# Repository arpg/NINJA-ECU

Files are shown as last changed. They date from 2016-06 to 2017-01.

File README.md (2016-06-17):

# NINJA-ECU
ECU board in order to control sensors and actuators of ARPG's self driving vehicle
## How board versions work?
each ECU pcb has a version format of **v.**_X_**.**_Y_ in which
* X represents the major change in functionality of the board
* Y represents minor changes like fixing errors in PCB or adding simple functions like an LED

## How to add a new board with major change?
* branch from current master (this should only add some readme files and folders)
* create your project in the folders created from previous step
* when you are ready to push your changes,create a new branch and name it as 'v.major_number' (ex. **v.3** )
* after you are done with your design add a minor tag of 1 to your last commit (ex. add tag **v.3.1**)

## How to add minor changes for last major board?
* apply andd commit your changes when you were done add a minor tag for your commit (ex. add tag **v.3.2**)

## What should every last minor commit include?
* updated pcbproject, schematic and layout files
* updated gerber files
* updated nc-drill files
* updated assembly files
* updated BOM
* updated pdf showing all schematic and layout files

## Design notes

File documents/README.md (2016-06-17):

# Documents
## what should be in this folder?
* a pdf documet showing all the schematics of the project and a 1:1 scaled layout with all layers

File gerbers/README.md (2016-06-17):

# Gerber Files
## what should be in this folder?
this folder should include all the gerber files and nc-drill files for the project

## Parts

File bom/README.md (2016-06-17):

# Bill Of Material
## what should be in this folder?
this folder includes a list of components with their designator, value, digikey part number, quantity and a short comment
try to use the template from ARPGPCBLib

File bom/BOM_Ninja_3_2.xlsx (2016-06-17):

Comment | Quantity | Designator | Manufacturer Part Number 1 | Supplier 1 | Supplier Part Number 1
Terminal3, Terminal2, Terminal2 | 3 | BLDC1, PWR1_BATT, PWR2_COMP |  |  | DNI
18pF | 2 | C1, C3 | 251R14S180GV4T | Digi-Key | 712-1321-1-ND
2.2uF | 9 | C2, C4, C6, C7, C25, C30, C34, C39, C46 | F981A225MMA | Digi-Key | 478-8647-1-ND
100nF | 23 | C5, C8, C9, C10, C11, C20, C21, C22, C35, C44, C48, C56, C63, C64, C65, C66, C67, C68, C69, C70, C71, C72, C73 | CC0603KRX7R7BB104 | Digi-Key | 311-1088-1-ND
15pF | 2 | C12, C13 | 251R14S150JV4T | Digi-Key | 712-1318-1-ND
4.7nF | 4 | C14, C15, C16, C17 | C1608C0G1E472J080AA | Digi-Key | 445-2712-1-ND
10uF | 5 | C18, C47, C49, C50, C54 | TAJC106M016RNJ | Digi-Key | 478-1702-1-ND
150uF | 1 | C19 | TCJW157M006R0070 | Digi-Key | 478-3481-1-ND
100uF | 1 | C23 | NOJC107M004RWJ | Digi-Key | 478-1824-1-ND
330uF | 1 | C24 | TAJC337M006RNJ | Digi-Key | 478-8902-1-ND
100pF | 2 | C26, C41 | C0603C101J5GACTU | Digi-Key | 399-1061-1-ND
150uF/6.3V | 1 | C27 | TCJW157M006R0070 | Digi-Key | 478-3481-1-ND
1000uF/16V | 2 | C28, C31 | UCL1C102MNL1GS | Digi-Key | 493-3930-1-ND
1nF | 2 | C29, C42 | GRM188R71H102KA01D | Digi-Key | 490-1494-1-ND
10nF | 2 | C32, C45 | CC0603KRX7R9BB103 | Digi-Key | 311-1085-1-ND
6.8nF | 1 | C33 | C1608C0G1E682J080AA | Digi-Key | 445-2667-1-ND
120pF | 1 | C36 | C0603C121J5GACTU | Digi-Key | 399-1062-1-ND
22nF | 1 | C38 | C0603C223K1RACTU | Digi-Key | 399-3476-1-ND
100uF/16V | 1 | C40 | TPSC107K010R0150 | Digi-Key | 478-7995-1-ND
15nF | 1 | C43 | C0603C153J3GACTU | Digi-Key | 399-10044-1-ND
220nF | 3 | C51, C52, C53 | C1608X7R1C224K080AC | Digi-Key | 445-1318-1-ND
220uF/16V | 1 | C55 | TPSC227K006R0125 | Digi-Key | 478-1768-1-ND
100uF | 1 | C57 | TPSC107K010R0150 | Digi-Key | 478-7995-1-ND
4.7uF | 2 | C58, C60 | TAJC475K035RNJ | Digi-Key | 478-1717-1-ND
27pF | 2 | C59, C62 | C0603C270F5GACTU | Digi-Key | 399-7888-1-ND
3.3uF | 1 | C61 | C1608X5R1A335K080AC | Digi-Key | 445-5168-1-ND
2.2nF | 1 | C74 | GRM1885C1H222JA01D | Digi-Key | 490-1459-1-ND
1N5821 | 2 | D1, D3 | 1N5821G |  | DNI
1N5819 | 1 | D2 | 1N5819HW-7-F | Digi-Key | 1N5819HW-FDICT-ND
Enc3, Enc2, Enc1, Enc4, USB1 | 5 | H1, H2, H3, H11, H19 | 0533980471 | Digi-Key | WM7608CT-ND
JTAG | 1 | H4 | 20021121-00010C4LF | Digi-Key | 609-3695-1-ND
Serv1, P_Servo, Serv2, Serv3, Serv4 | 5 | H5, H6, H13, H14, H15 |  |  | DNI
Pot1, Pot2, Pot3, Pot4, Pot5, Pot6, Oc1 | 7 | H7, H8, H9, H10, H12, H16, H17 | 0533980371 | Digi-Key | WM7607CT-ND
Hall Sens1, GPS_Con | 2 | H18, H20 | B6B-ZR-SM4-TF(LF)(SN) | Digi-Key | 455-1685-1-ND
IMU_Con | 1 | H21 | 0533980671 | Digi-Key | WM7610CT-ND
10uH | 2 | L1, L2 | LBR2012T100K | Digi-Key | 587-2045-1-ND
100uH | 1 | L3 | SDR0805-101KL | Digi-Key | SDR0805-101KLCT-ND
22uH | 1 | L4 | SDR0805-220ML | Digi-Key | SDR0805-220MLCT-ND
?H | 2 | L5, L6 | FBMJ2125HL8R0NT | Digi-Key | 587-1764-1-ND
LEDR | 3 | LED1, LED5, LED6 | LS R976-NR-1 | Digi-Key | 475-1278-1-ND
LEDY | 2 | LED2, LED4 | LY R976-PS-36 | Digi-Key | 475-2560-1-ND
LEDG | 1 | LED3 | LG R971-KN-1 | Digi-Key | 475-1410-1-ND
IRFS7530 | 6 | Q1, Q2, Q3, Q4, Q5, Q6 | IRFS7530-7PPBF | Digi-Key | IRFS7530-7PPBF-ND
120 | 10 | R1, R2, R3, R4, R9, R10, R17, R21, R69, R70 | RMCF0603JT120R | Digi-Key | RMCF0603JT120RCT-ND
4.7K | 4 | R5, R6, R7, R61 | ERJ-3GEYJ472V | Digi-Key | P4.7KGCT-ND
1K | 4 | R8, R63, R84, R85 | ERJ-3GEYJ102V | Digi-Key | P1.0KGCT-ND
180 | 6 | R11, R13, R15, R18, R23, R30 | RMCF0603JT180R | Digi-Key | RMCF0603JT180RCT-ND
330 | 12 | R12, R14, R16, R19, R24, R28, R29, R31, R41, R42, R43, R68 | RC0603JR-07330RL | Digi-Key | 311-330GRCT-ND
470 | 5 | R20, R22, R33, R35, R87 | RC0603JR-07470RL | Digi-Key | 311-470GRCT-ND
10K | 12 | R25, R26, R27, R44, R45, R46, R48, R50, R58, R59, R60, R62 | ERJ-3GEYJ103V | Digi-Key | P10KGCT-ND
2.2K | 4 | R32, R34, R36, R57 | RMCF0603JT2K20 | Digi-Key | RMCF0603JT2K20CT-ND
560 | 2 | R37, R67 | RC0603FR-07560RL | Digi-Key | 311-560HRCT-ND
510K | 1 | R38 | ERJ-3EKF5103V | Digi-Key | P510KHCT-ND
90.9K | 1 | R39 | ERJ-3EKF9092V | Digi-Key | P90.9KHCT-ND
3.09K | 1 | R40 | ERJ-3EKF3091V | Digi-Key | P3.09KHCT-ND
330K | 1 | R47 | ERJ-3GEYJ334V | Digi-Key | P330KGCT-ND
15K | 1 | R49 | RMCF0603JT15K0 | Digi-Key | RMCF0603JT15K0CT-ND
220K | 1 | R51 | ERJ-3GEYJ224V | Digi-Key | P220KGCT-ND
3.3K | 1 | R52 | RMCF0603JT3K30 | Digi-Key | RMCF0603JT3K30CT-ND
18K | 2 | R53, R56 | RMCF0603JT18K0 | Digi-Key | RMCF0603JT18K0CT-ND
1M | 2 | R54, R55 | ERJ-3EKF1004V | Digi-Key | P1.00MHCT-ND
12K | 1 | R64 | RC0603JR-0712KL | Digi-Key | 311-12KGRCT-ND
DNI | 2 | R65, R66 |  |  | DNI
4.7 | 6 | R71, R72, R75, R77, R80, R81 | RC0603JR-074R7L | Digi-Key | 311-4.7GRCT-ND
39K | 6 | R73, R74, R76, R78, R82, R83 | RC0603FR-0739KL | Digi-Key | 311-39.0KHRDKR-ND
0.001 | 2 | R79, R86 | WSLP59311L000FEB | Digi-Key | WSLPD-.001CT-ND
SW_TACT | 1 | S1 | PTS645SH50SMTR92 LFS | Digi-Key | CKN9085CT-ND
BC817 | 2 | T1, T2 | BC817-25LT1G | Digi-Key | BC817-25LT1GOSCT-ND
STM32F207VCT6 | 1 | U1 | STM32F207VCT6 | Digi-Key | 497-11170-ND
DRV8302 | 1 | U2 | DRV8302DCAR | Digi-Key | 296-29544-6-ND
1117-3.3 | 2 | U3, U5 | LM1117IMPX-3.3/NOPB | Digi-Key | LM1117IMPX-3.3/NOPBCT-ND
LTM8026 | 1 | U4 | LTM8026EV#PBF | Digi-Key | LTM8026EV#PBF-ND
AT93C46DN-SP25-B | 1 | U6 | AT93C46DN-SH-B | Digi-Key | AT93C46DN-SH-B-ND
FT4232HQ-Reel | 1 | U7 | FT4232HQ-REEL | Digi-Key | 768-1027-1-ND
MAX3485 | 1 | U8 | MAX3485CSA+ | Digi-Key | MAX3485CSA+-ND
MPU9150 | 1 | U9 | MPU-9150 | Digi-Key | 1428-1009-1-ND
8MHz | 1 | X1 | ABM7-8.000MHZ-D2Y-T | Digi-Key | 535-9831-1-ND
32768 Hz | 1 | X2 | ABS06-107-32.768KHZ-T | Digi-Key | 535-12373-1-ND
12MHz | 1 | X3 | ABM7-12.000MHZ-B4-T | Digi-Key | 535-13457-1-ND

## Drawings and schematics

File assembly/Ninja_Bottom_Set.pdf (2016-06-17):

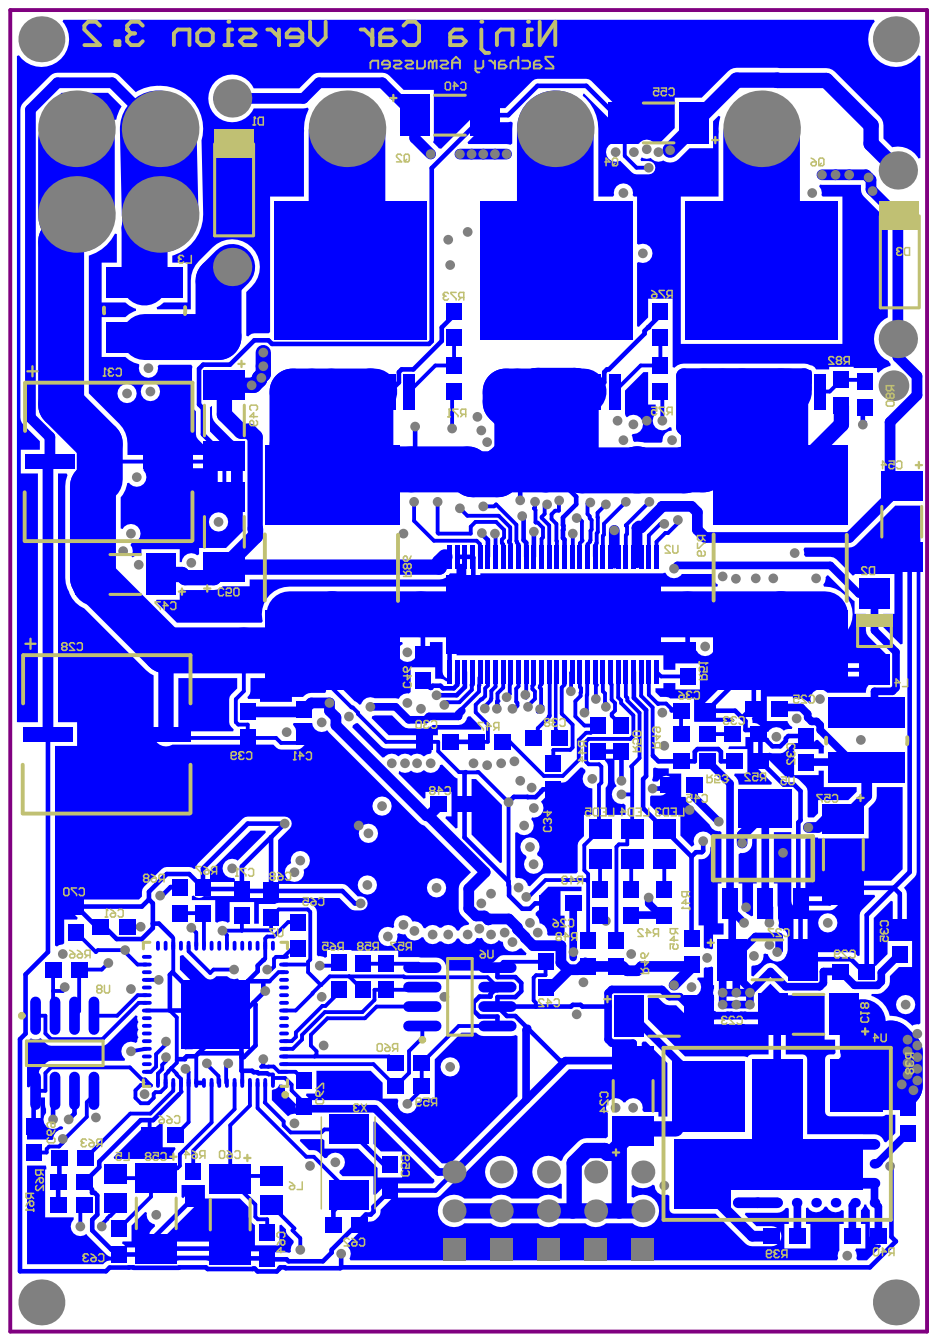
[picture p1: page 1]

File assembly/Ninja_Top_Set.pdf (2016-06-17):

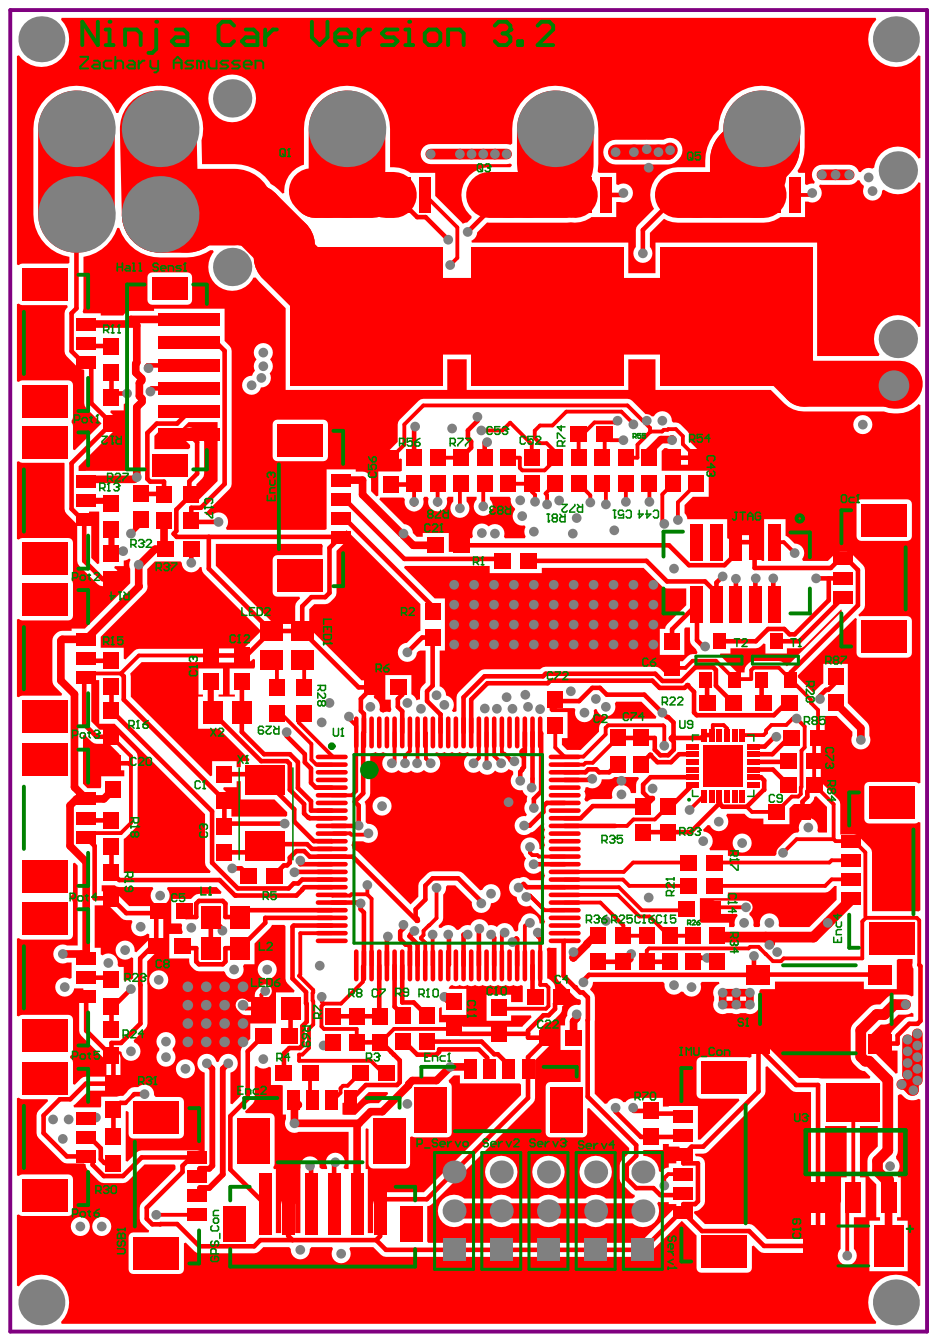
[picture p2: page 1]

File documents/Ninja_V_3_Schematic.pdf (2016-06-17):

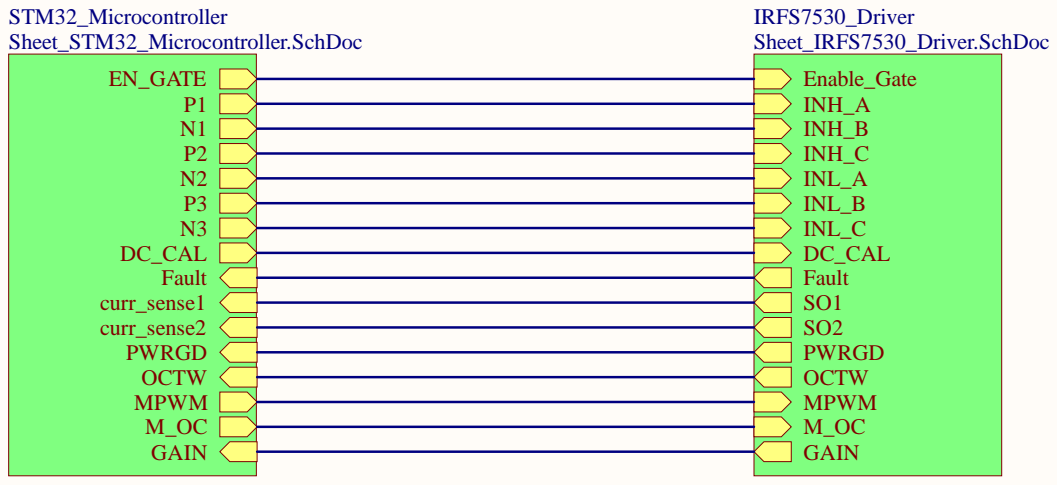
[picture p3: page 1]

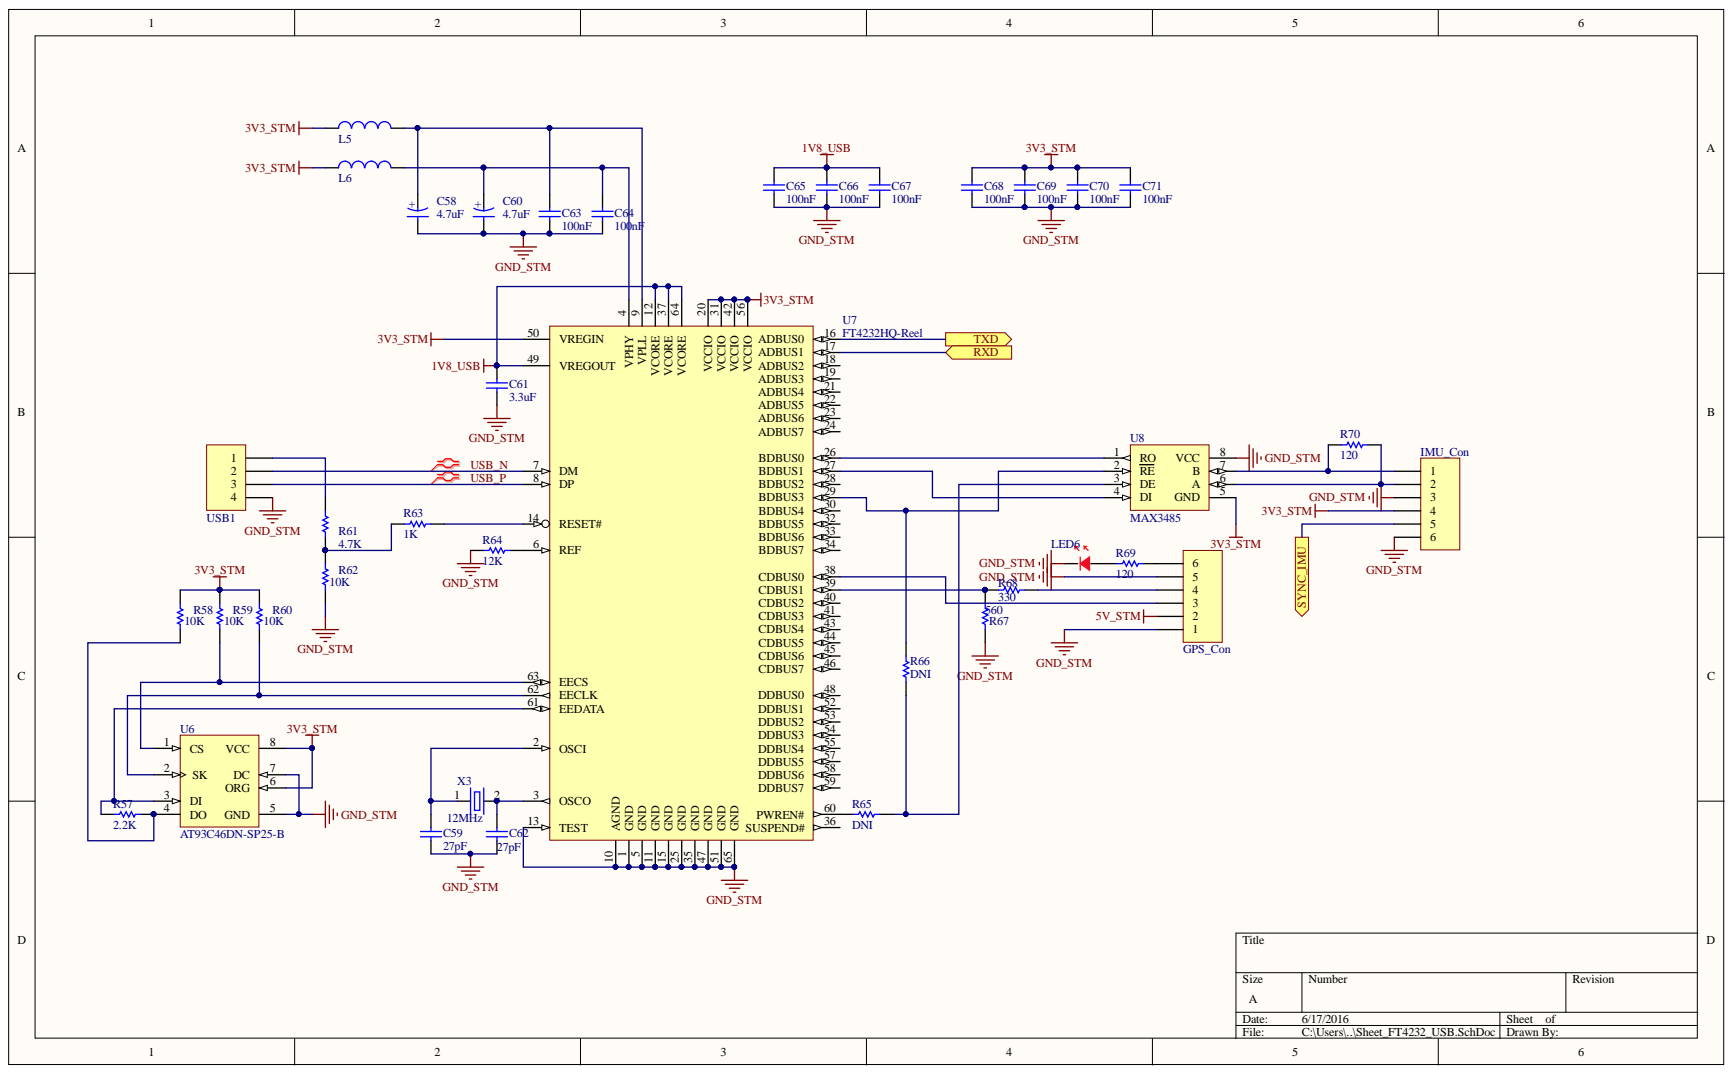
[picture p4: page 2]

EECLK 62
EEDATA 61

U6 3V3_STM | OSCI 2

SK 2 ORG | 6 DC 7 | | OSCO 3

Size A | Number | Revision

Date: 6/17/2016 | Sheet of
File: C:\Users\..\Sheet_FT4232_USB.SchDoc | Drawn By:

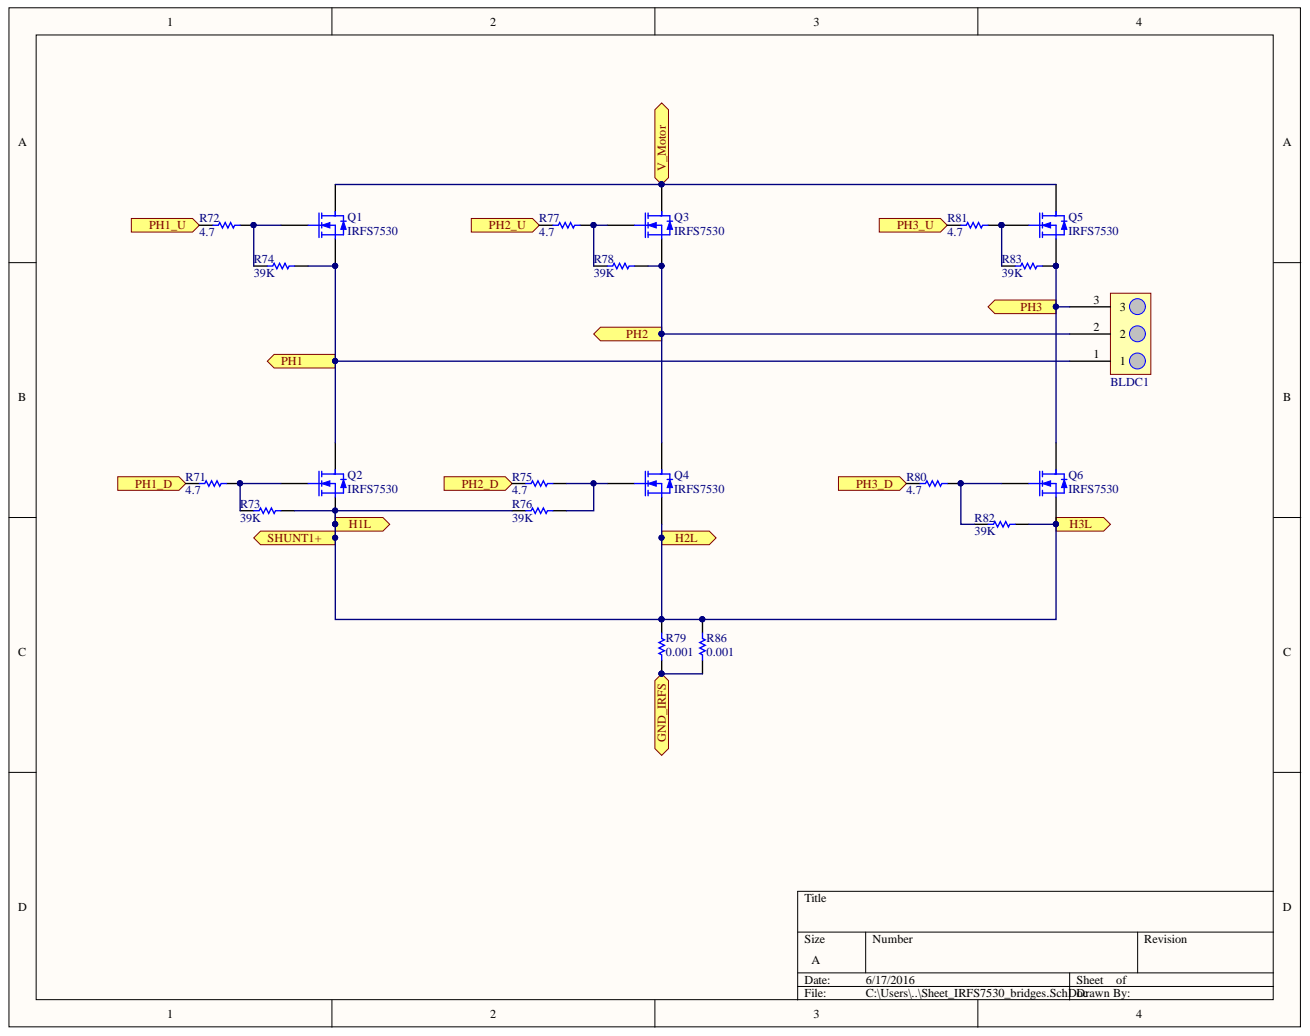
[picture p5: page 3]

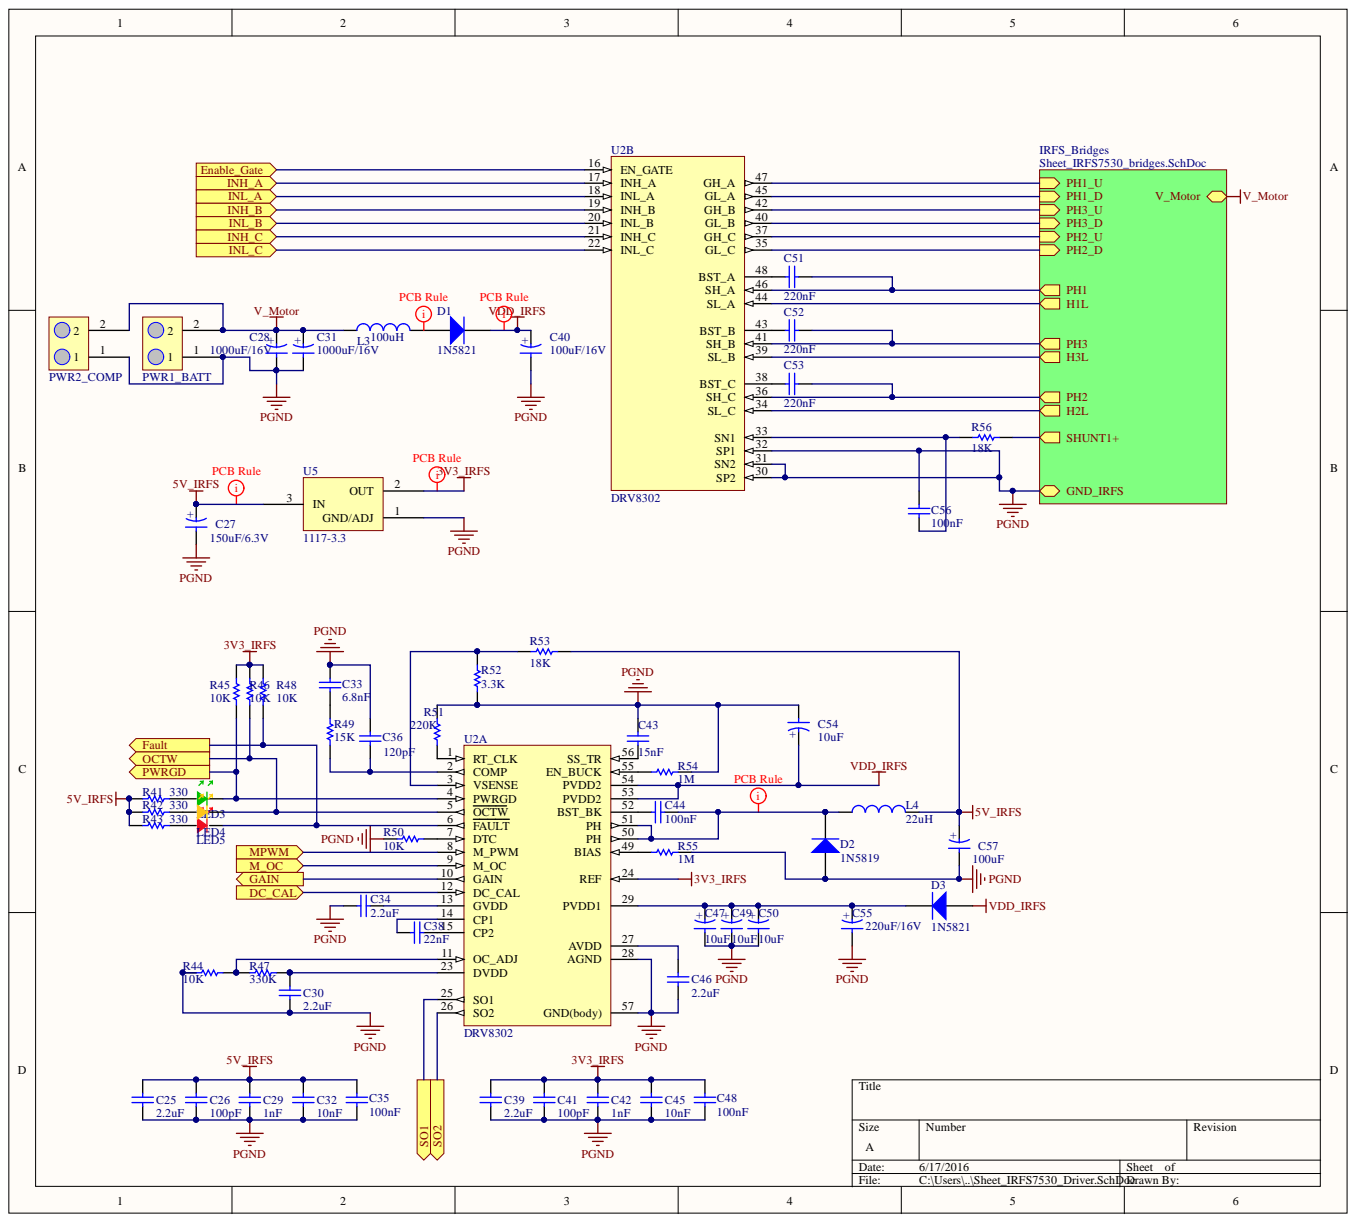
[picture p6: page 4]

RT_CLK 1

10K | M_PWM 8 | R55

R47 | DVDD 23

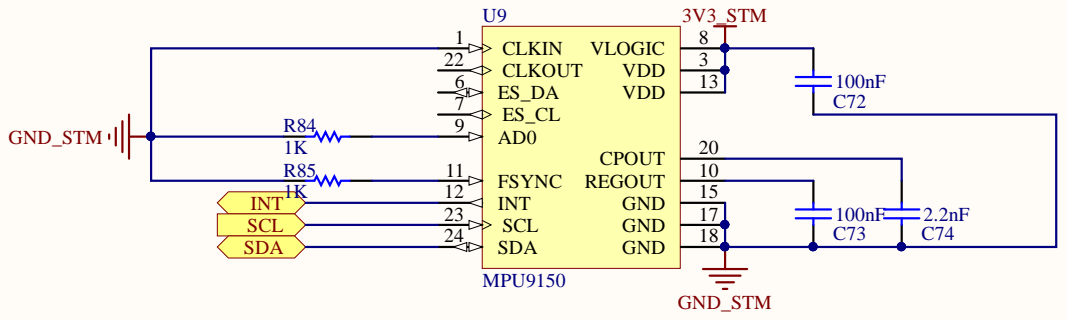
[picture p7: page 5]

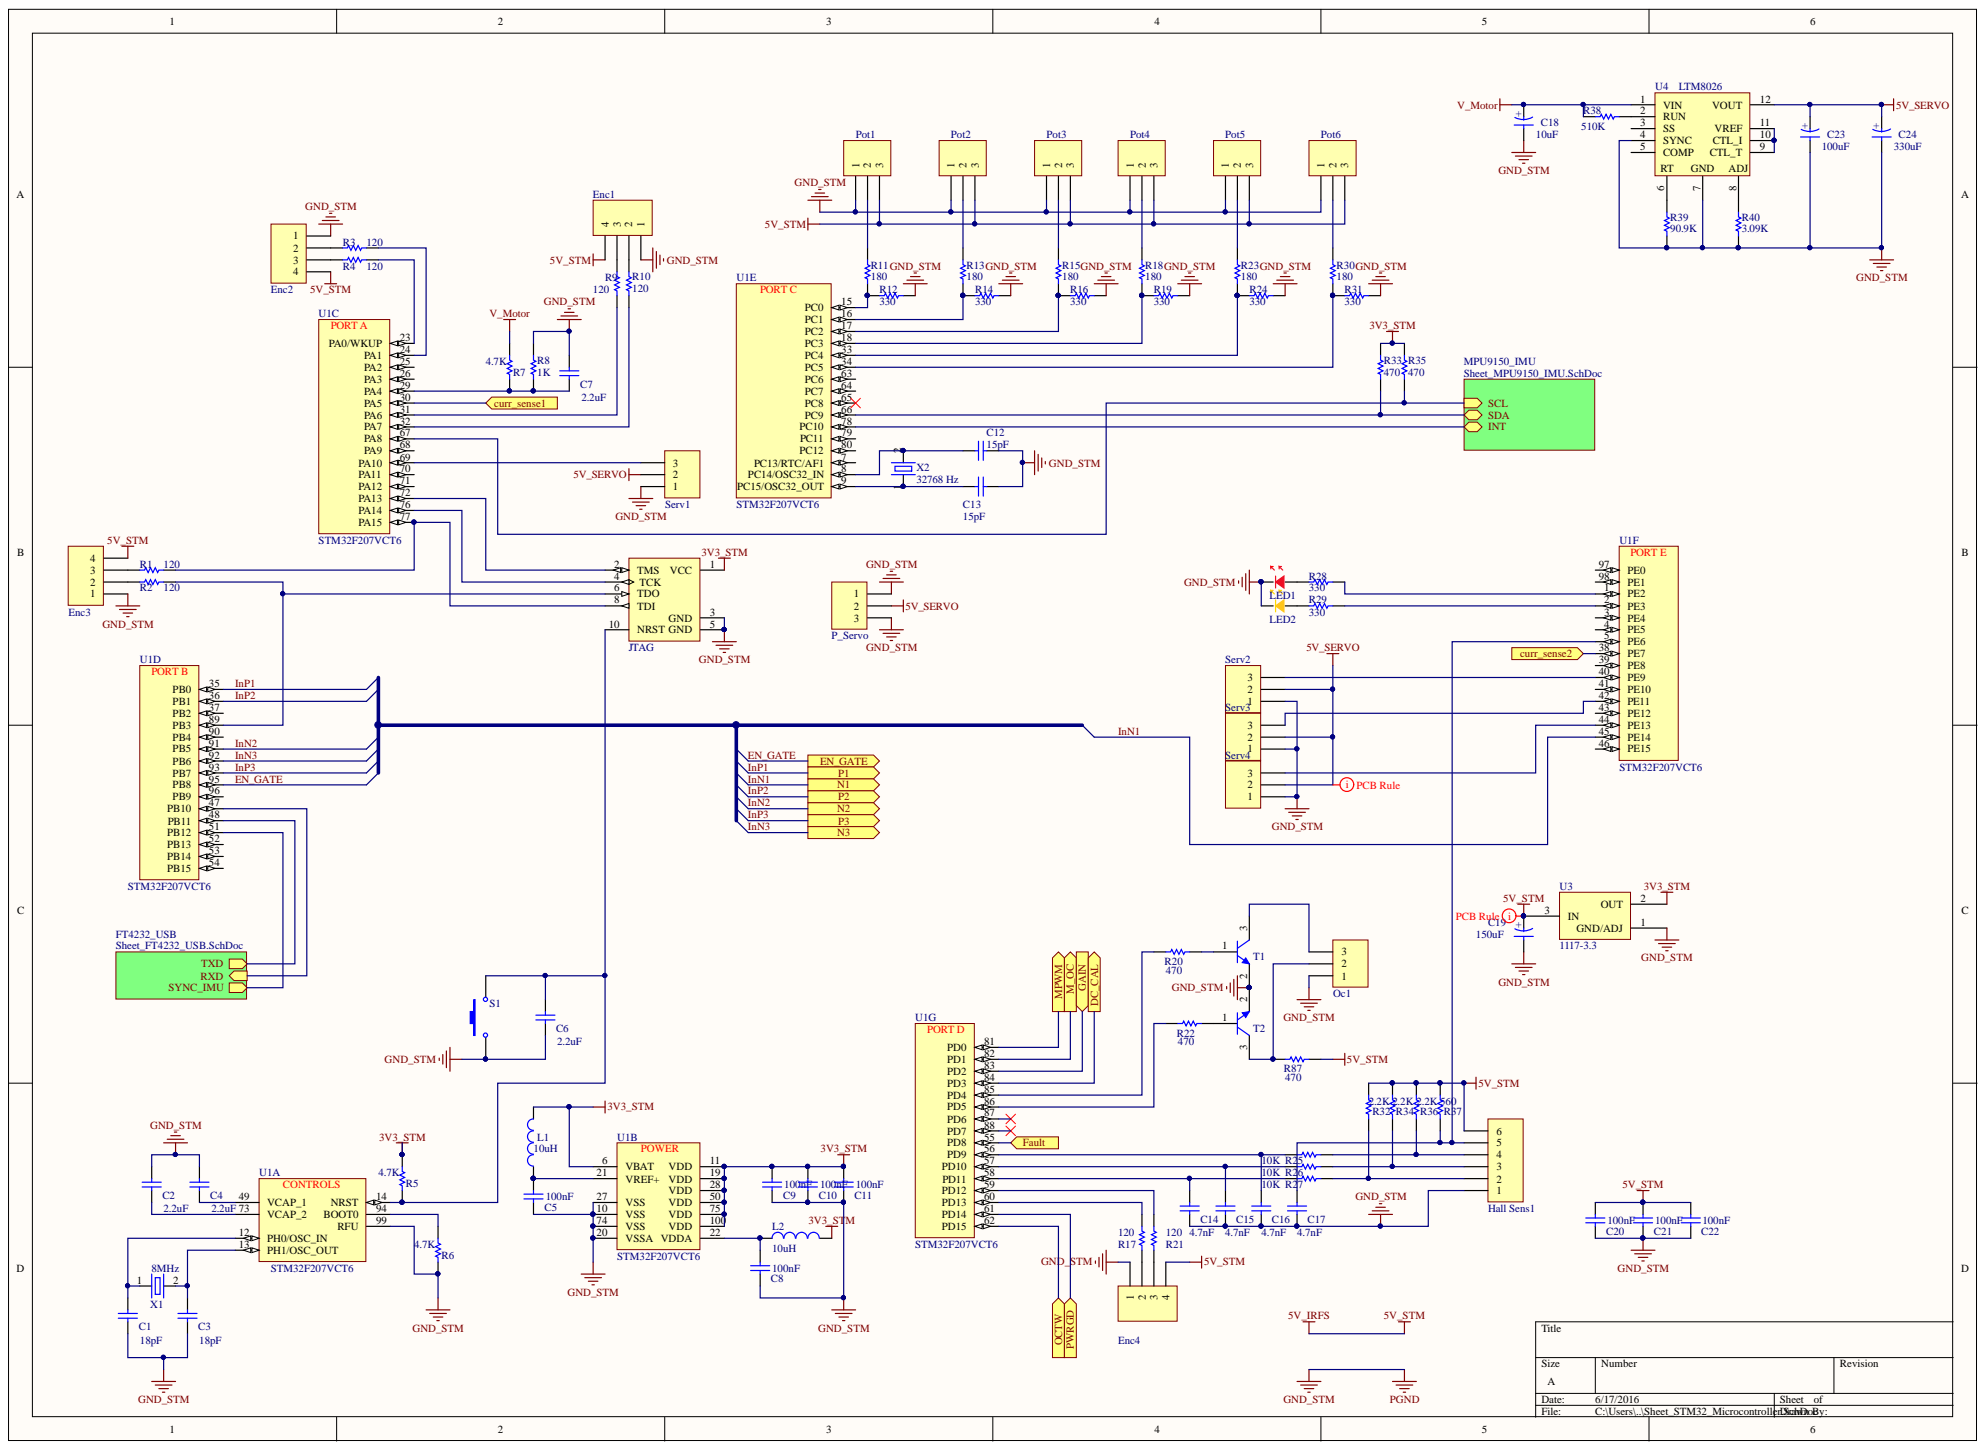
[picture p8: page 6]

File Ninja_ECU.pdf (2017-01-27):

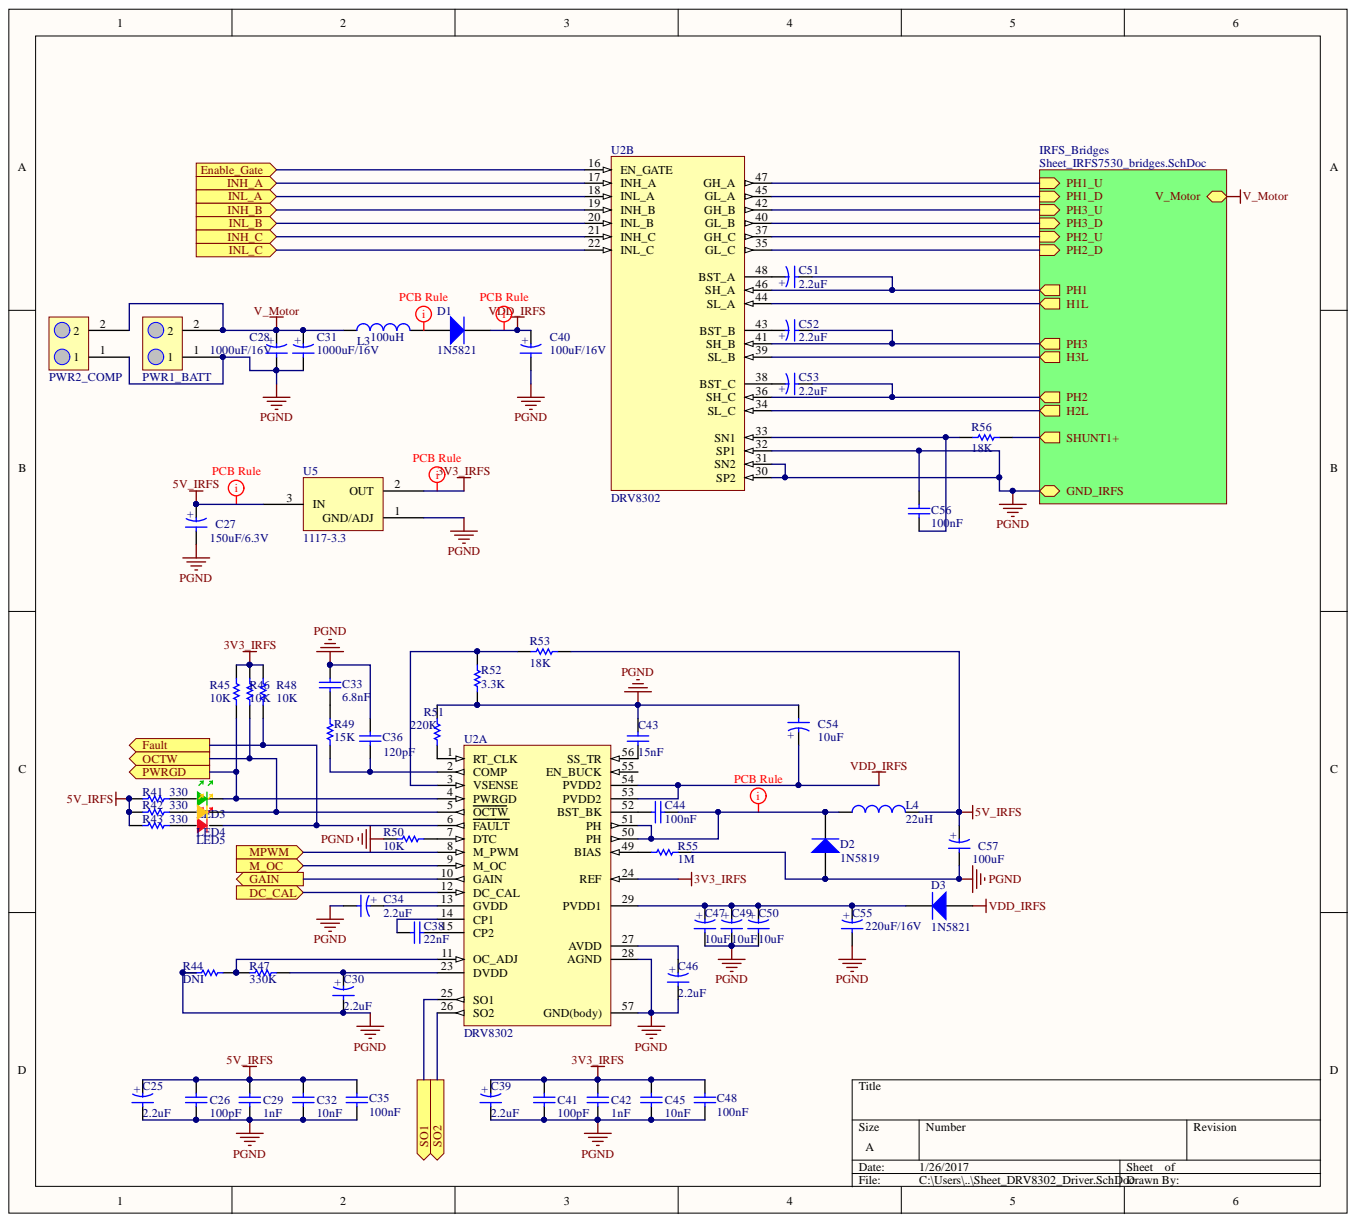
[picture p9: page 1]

10K | M_PWM 8 | R55

R47 | DVDD 23

Date: 1/26/2017 | Sheet of
File: C:\Users\..\Sheet_DRV8302_Driver.SchDoDr c awn By:

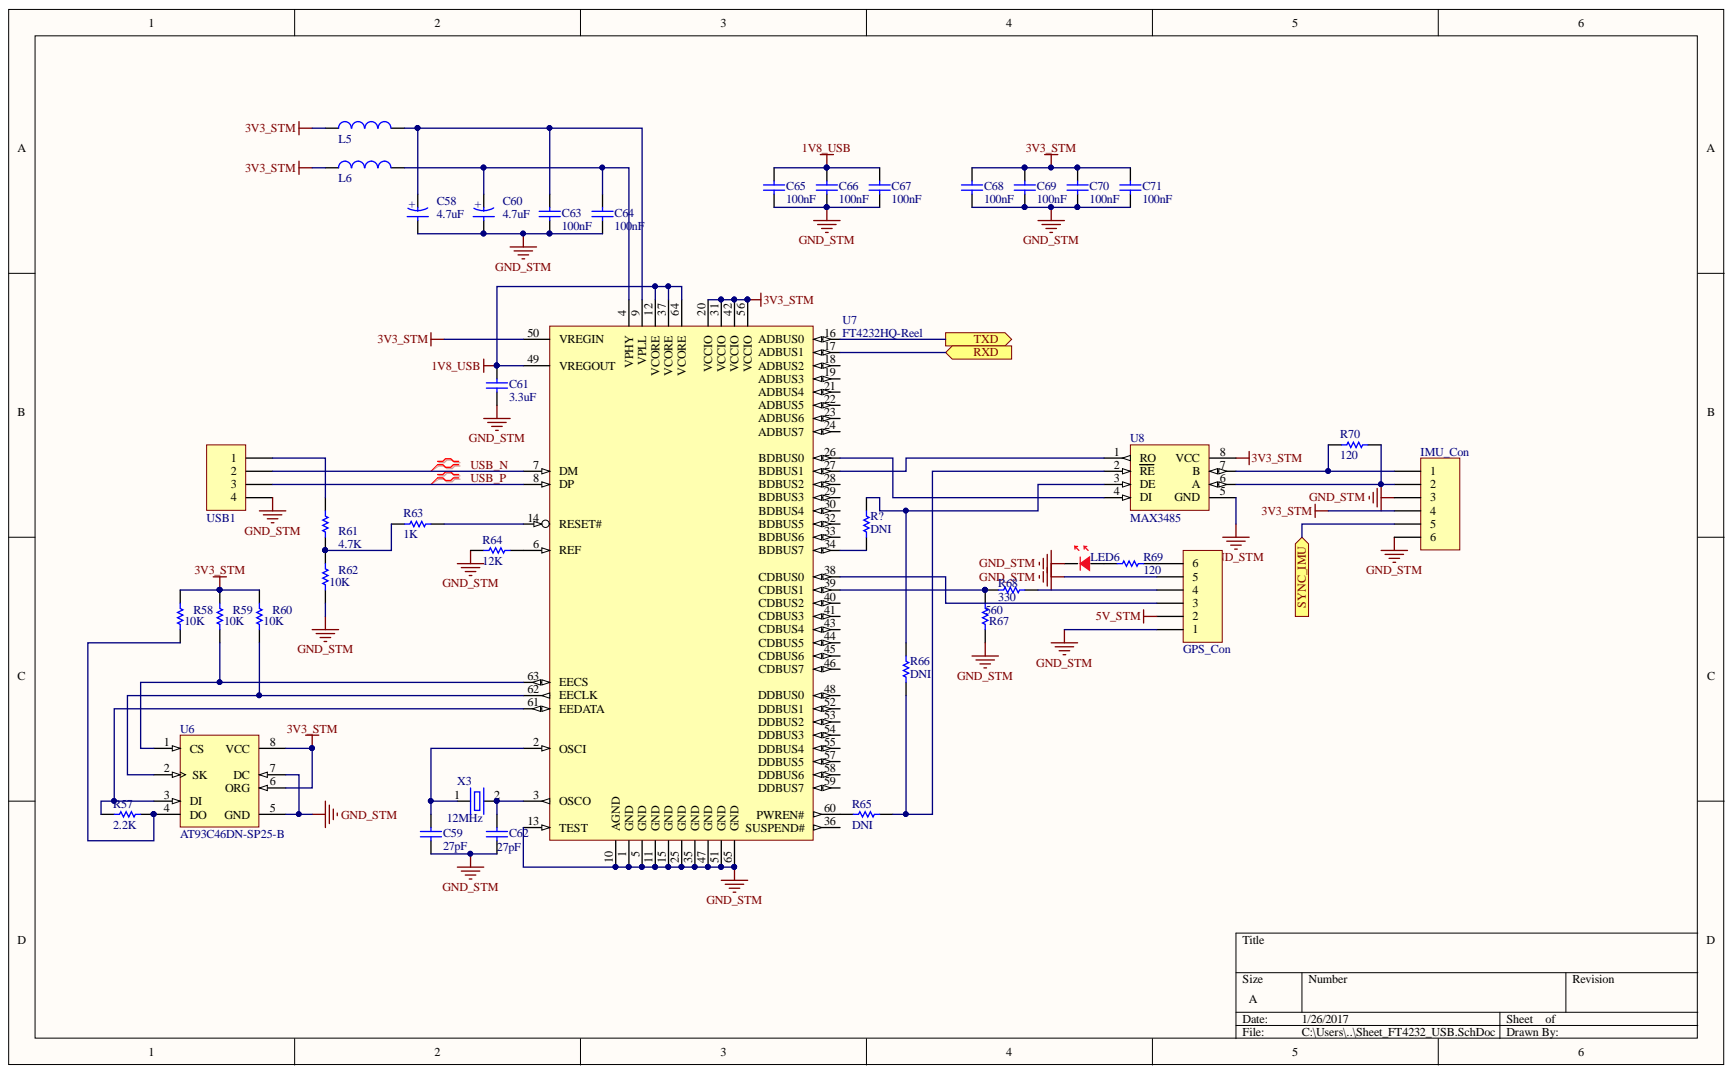
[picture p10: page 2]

EECLK 62
EEDATA 61

U6 3V3_STM | OSCI 2

SK 2 ORG | 6 DC 7 | | OSCO 3

Size A | Number | Revision

Date: 1/26/2017 | Sheet of
File: C:\Users\..\Sheet_FT4232_USB.SchDoc | Drawn By:

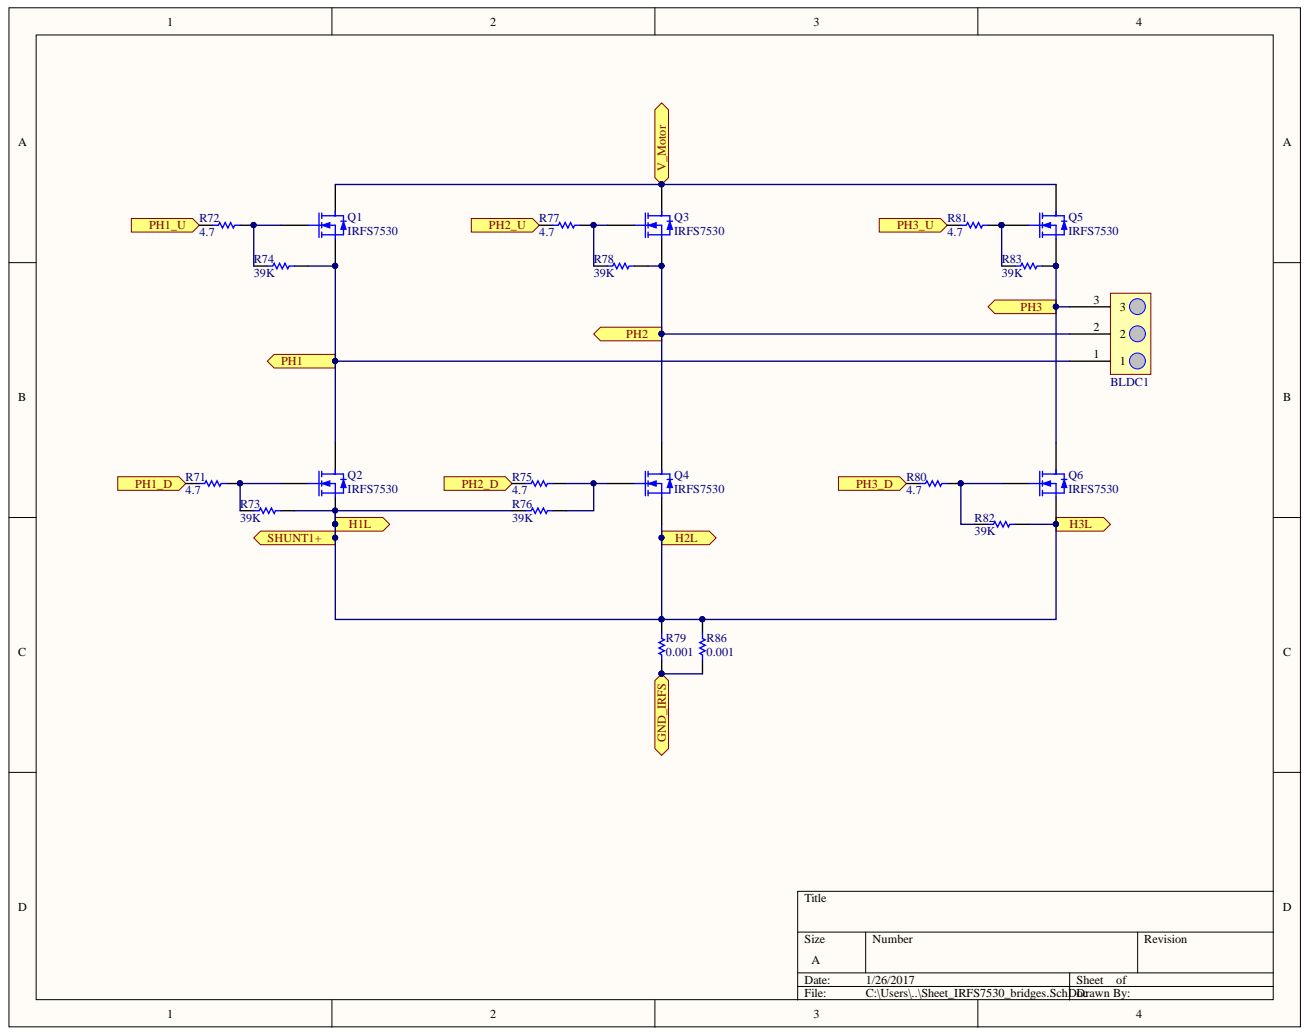
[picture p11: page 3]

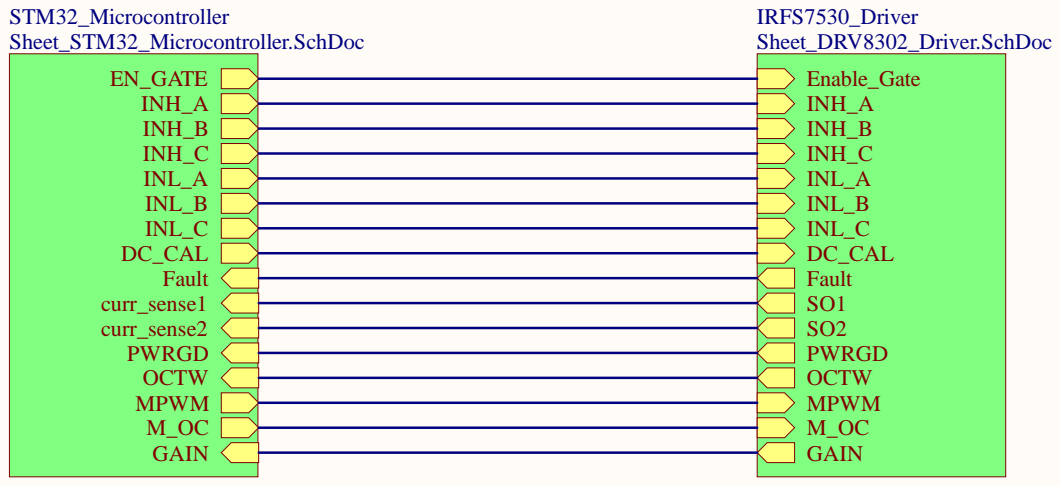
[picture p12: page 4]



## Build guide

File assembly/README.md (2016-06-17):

# Assembly files
## what should be in this folder?
this folder should include only the following files
* component placement file (witn coordinates of components, their orientation, and layer)
* an image of Top/Bottom(mirrored) overlayer which shows where each component goes

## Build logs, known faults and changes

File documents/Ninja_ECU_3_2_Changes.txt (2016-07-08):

Ninja ECU 3.2 Changes

-This document is a list of physical hardware changes we need to make to each board in order for it to work, specific to ECU 3.2.
The actual errors are lised in the text document name "Ninja_ECU_Errors" in this same folder.These are the soldering changes and 
fixes we made on the first board and need to apply to the other three.

1. Using an exacto knife, cut the line connecting pin 18 of the DRV chip to its nearby via. Solder a wire directly to pin 18, this
wire needs to be quite long as it needs to wrap around the board to the microcontroller
2. There are two resistors connecting encoder 4 to the microcontroller pins 59 and 60. Desolder these resistors and move them to 
the right so that only one end of the resistor is on the right pad and the other is not connected.
3. Solder the other end of the DRV wire to the now empty pad that connects to pin 60 of the microcontroller. The PWM signal is fixed.
4. Solder a wire to the unconnected side of R21 and connect it to pin 63 of the microcontroller. 
5. Solder-bridge 64 and 65 together to make connecting the other resistor easier. Do the same process to connect R17 to the pin 64
and pin 65 bridge. We must not use pin 65. Now we have our encoder back.
6. For the FT4232 we need to switch the lines coming from 26 and 27 of the FTDI chip. Cut the line, shave off the mask, and solder
a wire to the exposed track. Do for both lines.
7. Connect the pin 27 line to pin 1 of the MAX and connect the pin 26 line to pin 4 of the MAX.
8. Desolder pins 5 and 8 of the MAX and lift them off their pads.
9. Solder a wire to pin 5, scrape off the mask from the ground plane just above this pin, and solder the other end of the wire to
the exposed polygon.
10. Solder a wire to pin 8 of the MAX and solder the other end to the nearby 3.3V via.

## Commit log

2016-06-17 Added BOM's and Pick and Place files
    Added the pick and place file for Ninja Version 3's assembly. Added the
    Bill of Materials used for assembly along with its template.
    [BOM_Ninja_3_2.xlsx, Ninja_3_2_BOM_Template.xlsx]
2016-06-17 Added Gerbers and PDFs
    Changed gitignore to include PDF documents. Added the PDF documents of
    Ninja's schematic and 1:1 PCB files. Also added all the gerber files
    used to order the PCB print.
    [cam.drl, ninja_3_2_pcb.gbl, ninja_3_2_pcb.gbo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]
2016-06-23 Added Sheets and PCB files
    Added in all of the sheets for the Ninja ECU v.3.2 along with the PCB
    file
    [Ninja_ECU_PCB.PcbDoc, Sheet_DRV8302_Driver.SchDoc, Sheet_FT4232_USB.SchDoc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]
2016-06-23 Moved gerbers and removed template
    [Ninja_3_2_BOM_Template.xlsx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]
2016-06-23 Added Project File
    [Ninja_ECU.PrjPcb]
2016-06-23 Fixed USB signal problem and micro PWM problem
    USB signals on pin 26 and 27 were swapped. The transceive and receive
    signals were wrong connecting to U8. Started fixing the problem with the
    motor PWM signals (need to check with Akshay first). Before, they were
    on different timers for the PWM signals which is wrong
    [Sheet_FT4232_USB.SchDoc, Sheet_STM32_Microcontroller.SchDoc]
2016-06-23 Fixed PWM signal matching
    PWM signals are now correct and synced with firmware
    [Sheet_STM32_Microcontroller.SchDoc]
2016-06-29 Nothing really changed
    [Sheet_STM32_Microcontroller.SchDoc]
2016-07-05 Just checked cap orientations
    [Ninja_ECU_PCB.PcbDoc, Sheet_STM32_Microcontroller.SchDoc]
2016-07-06 More updates
    [Ninja_ECU.PrjPcb, Ninja_ECU_PCB.PcbDoc, Sheet_Ninja_ECU.SchDoc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]
2016-07-08 Fixed errors
    MAX3485 had GND connected to VCC and vice versa. Fixed syntax error on
    the Sheet_Ninja_ECU sheet stated in error document.
    [Sheet_FT4232_USB.SchDoc, Sheet_Ninja_ECU.SchDoc, Sheet_STM32_Microcontroller.SchDoc]
2016-07-11 Rearranged some pins to match firmware
    [Ninja_ECU_PCB.PcbDoc, Sheet_STM32_Microcontroller.SchDoc]
2016-08-08 Changed capacitor
    [Sheet_DRV8302_Driver.SchDoc]
2016-08-08 Changed caps
    [Sheet_DRV8302_Driver.SchDoc]
2016-09-04 Nothing happened
    [Sheet_DRV8302_Driver.SchDoc, Sheet_FT4232_USB.SchDoc, Sheet_STM32_Microcontroller.SchDoc]
2016-10-18 Nothing changed
    [Ninja_ECU.PrjPcb, Ninja_ECU_PCB.PcbDoc]
2016-11-30 No change
    [Ninja_ECU_PCB.PcbDoc]
2017-01-27 Made final changes and layout changes for next board
    Fixed the USB problems we had as well as synced the firmware with out
    pin layout. Then changed the layout to match the design
    [Ninja_ECU.PrjPcb, Ninja_ECU_PCB.PcbDoc, Sheet_DRV8302_Driver.SchDoc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]
2017-01-30 added bypass cap to ftdi chip's reset pin
    [Ninja_ECU.PrjPcb, Ninja_ECU_PCB.PcbDoc, Sheet_FT4232_USB.SchDoc]
